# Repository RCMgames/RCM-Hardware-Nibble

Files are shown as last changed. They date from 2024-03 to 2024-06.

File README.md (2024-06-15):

# RCM-Hardware-Nibble
v1.8

Half a [BYTE](https://github.com/RCMgames/RCM-Hardware-BYTE)

* 1.08 by 1.12 inches, 27.432 by 28.448 millimeters
* 4 motors
* 4 servos
* 2 additional GPIO pins
* built-in [IMU](https://github.com/RCMgames/useful-code/blob/main/sensors/IMUs/ICM20948/ICM20948_helper.h)
* battery monitoring
* I2C connector on QT PY
* runs on 3-11 volts

program with [RCMv2](https://github.com/RCMgames/RCMv2)

### Tested with the following types of ESP32 QT Py:
| Type of QT Py | PlatformIO name | link to Adafruit |
| --- | --- | --- |
| S3 with 2MB PSRAM |  adafruit_qtpy_esp32s3_n4r2 |  https://www.adafruit.com/product/5700 |
| S3 with 8Mb Flash |  adafruit_qtpy_esp32s3_nopsram |  https://www.adafruit.com/product/5426 |
| S2 |  adafruit_qtpy_esp32s2 |  https://www.adafruit.com/product/5325  |

Look here for how to program it: https://github.com/RCMgames/RCMv2

Look here for more information and examples of robots: https://github.com/rcmgames

Want slightly larger and 8 motors and 8 servos? Look at the [BYTE](https://github.com/rcmgames/RCM-Hardware-BYTE)

## Options for purchasing

* [PCBWay link](https://www.pcbway.com/project/shareproject/RCMhardwareNibble_v1_8_dbf51cb4.html) (PCBWay will give me a commission without increasing the price for you). (approximately $110 for 2 boards and manufacturing took a month).
* send the gerbers, bill of materials, and ComponentPlacement files (in /PCBproduction-RCM-Nibble) to a PCB manufacturer of your choice (details you may be asked for: min hole 0.25mm, min track/spacing 5/5mil, thickness 1.0mm, 1 oz Cu outer 1.5 oz Cu inner, tell them to not solder the icm20948's exposed pad)

## Components
Solder by hand to complete the assembly of your boards.
| part | links | quantity | notes |
| ----- | ----- | ----- | ----- |
| RCM Nibble circuit board | [options for purchasing](https://github.com/RCMgames/RCM-Hardware-Nibble/tree/main#options-for-purchasing) | 1 | |
| ESP32 QT Py | [compatible QT Py](https://github.com/RCMgames/RCM-Hardware-Nibble/tree/main#tested-with-the-following-types-of-esp32-qt-py) | 1 | |
| 2x4 female header pins | [this](https://www.digikey.com/en/products/detail/sullins-connector-solutions/PPPC042LFBN-RC/810244) or 2 strips of 4 | 1 | for motors |
| 7 female header pins | | 2 | for QT Py |
| 3 male header pins | | 4 | for servos |
| 2 male header pins | | 2 | for extra GPIO pins |
| battery wires | JST RCY OR 9V battery snap | 1 | [Amazon JST RCY](https://www.amazon.com/dp/B00Z04QFN2/) |
| servo buck boost 5v 2A | [Pololu](https://www.pololu.com/product/4085) | 0 or 1 | if you want to supply voltages above or below what servos can accept (supplies other than 5AAs) |

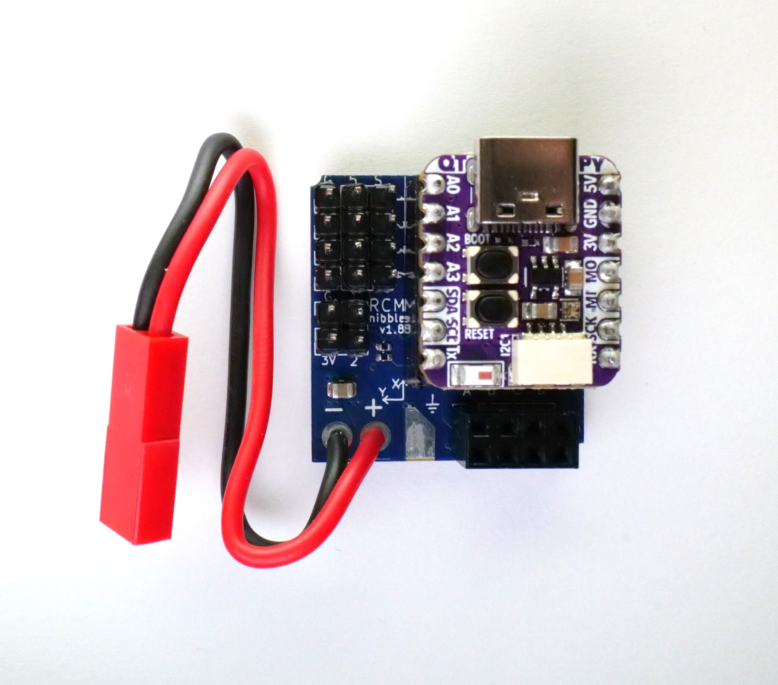
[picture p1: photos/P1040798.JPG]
photos

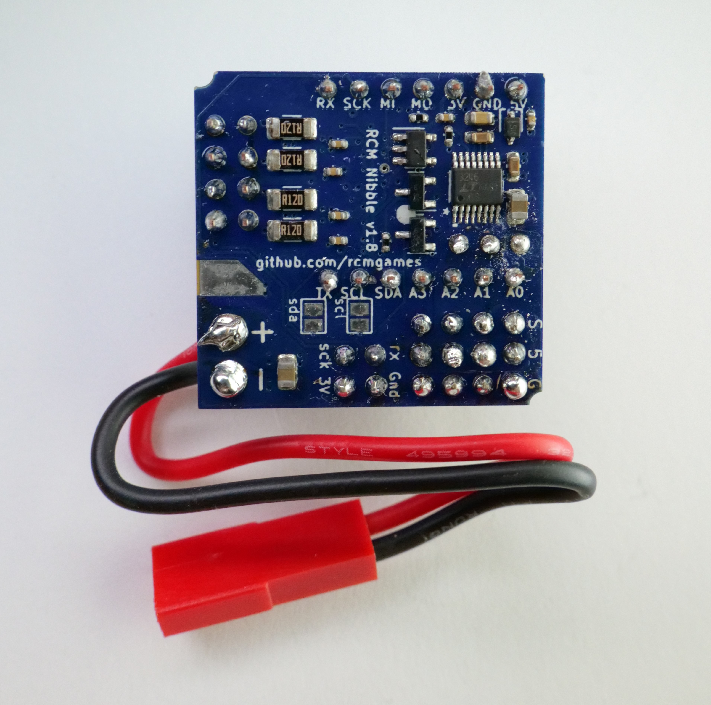
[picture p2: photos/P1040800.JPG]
photos


## Acknowledgements
* I would like to thank [PCBWay](https://www.pcbway.com/) for sponsoring prototyping runs of this project. PCBWay produces very nice boards, supports open source hardware, and gave me great support as I worked on this project. Special thanks to Liam!

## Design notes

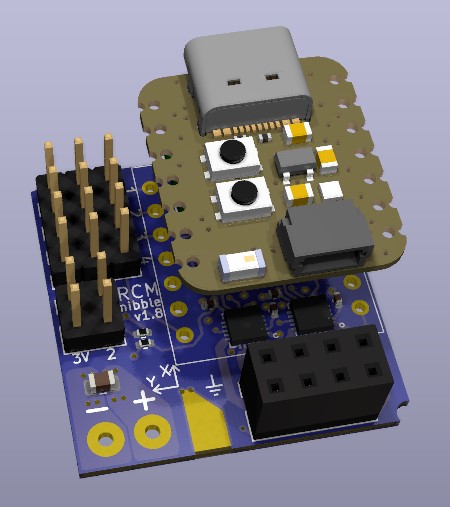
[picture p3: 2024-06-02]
CAD renders/render 1.jpg

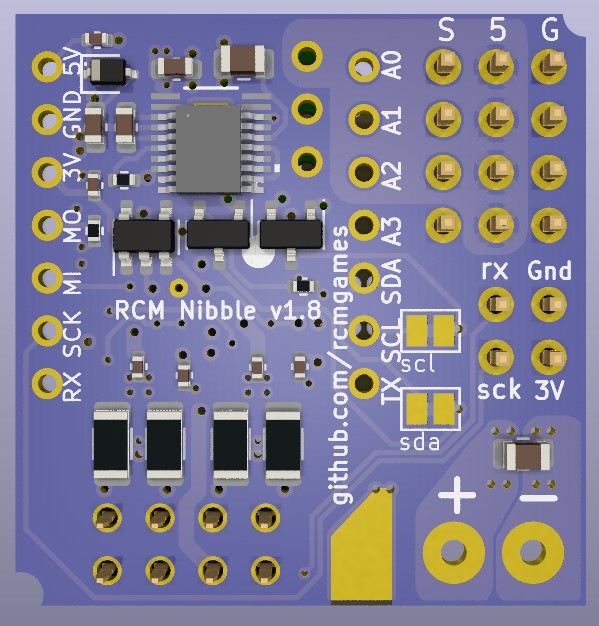
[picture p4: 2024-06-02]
CAD renders/bottom.jpg

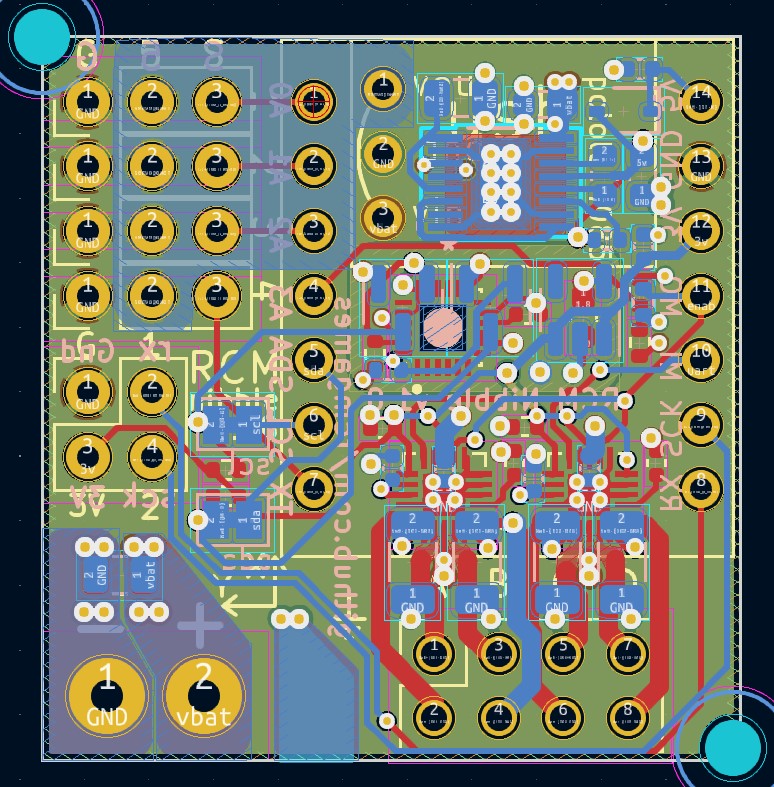
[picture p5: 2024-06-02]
CAD renders/kicad.jpg

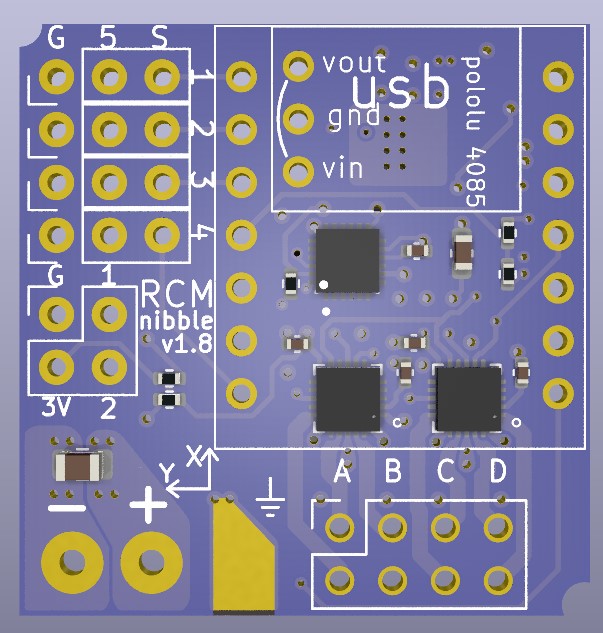
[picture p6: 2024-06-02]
CAD renders/top.jpg

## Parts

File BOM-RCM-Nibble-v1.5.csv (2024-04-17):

Reference | Value | Footprint | Datasheet | Manufacturer | Package | digikey part # | link | mount_type | mpn | Qty
C1, C3-C8, C11, C15, C17, C18 | 100nF/0402/16V/X7R/<=10%/ceramic | Capacitor_SMD:C_0402_1005Metric | ~ | any | 0402 | 4713-GMC04X7R104K50NTCT-ND | https://www.digikey.cn/en/products/detail/cal-chip-electronics-inc/GMC04X7R104K50NT/18151122 | smt | GMC04X7R104K50NT | 11
C2, C9, C16 | 22uF/0805/>=16V | Capacitor_SMD:C_0805_2012Metric | ~ | any | 0805 | 4713-GMC21X5R226M25NTCT-ND | https://www.digikey.cn/en/products/detail/cal-chip-electronics-inc/GMC21X5R226M25NT/18151071 | smt | GMC21X5R226M25NT | 3
C10, C13, C14 | 2.2uF/0603/>=16V | Capacitor_SMD:C_0603_1608Metric | ~ | any | 0603 | 4713-GMC10X7R225K16NTCT-ND | https://www.digikey.cn/en/products/detail/cal-chip-electronics-inc/GMC10X7R225K16NT/22461333 | smt | GMC10X7R225K16NT | 3
C12 | 22uF/0603/>=10V | Capacitor_SMD:C_0603_1608Metric | ~ | any | 0603 | 4713-GMC10X5R226M10NTCT-ND | https://www.digikey.cn/en/products/detail/cal-chip-electronics-inc/GMC10X5R226M10NT/22461275 | smt | GMC10X5R226M10NT | 1
D1 | 1A Zener Diode / >=1A / 600 mV Vf @ 1 A | Diode_SMD:D_SOD-323 | ~ | Good-Ark Semiconductor | D_SOD-323 | 4786-GDB5818WSCT-ND | https://www.digikey.com/en/products/detail/good-ark-semiconductor/GDB5818WS/18648294 | smt | GDB5818WS | 1
ESP32_QT_PY1 | microcontroller | !RCMhardware footprints:ESP32 QT PY | ~ | do not place or purchase for PCB assembly | tht | 1528-5426-ND or 1528-5700-ND |  | tht | do not place or purchase for PCB assembly | 1
H1, H2 | MountingHole | MountingHole:MountingHole_2.2mm_M2 | ~ | n/a | n/a | n/a | n/a | n/a | n/a | 2
IC1, IC2 | TMC7300 | !RCMhardware footprints:QFN-20-1EP_3x3mm_P0.4mm_EP1.65x1.65mm | https://www.analog.com/media/en/technical-documentation/data-sheets/TMC7300_datasheet_rev1.08.pdf | Analog Devices | QFN-20-1EP_3x3mm_P0.4mm_EP1.65x1.65mm | 175-TMC7300-LA-TCT-ND | https://www.digikey.com/en/products/detail/analog-devices-inc-maxim-integrated/TMC7300-LA-T/11483537 | smt | TMC7300-LA-T | 2
J1 | pads to solder wires to | !RCMhardware footprints:battery wires | JST RCY suggested | ~ | tht | ~ | https://www.amazon.com/dp/B00Z04QFN2/ | tht | do not place or purchase for PCB assembly | 1
J2-J5 | Conn_01x03 | Connector_PinHeader_2.54mm:PinHeader_1x03_P2.54mm_Vertical | ~ | ~ | tht | ~ | ~ | tht | do not place or purchase for PCB assembly | 4
J6 | 2x04 female header pins | !RCMhardware footprints:PinSocket_2x04_P2.54mm_Vertical | ~ | do not place or purchase for PCB assembly | tht | S7107-ND | https://www.digikey.com/en/products/detail/sullins-connector-solutions/PPTC082LFBN-RC/810214 | tht | do not place or purchase for PCB assembly | 1
J9 | Conn_02x02_Top_Bottom | Connector_PinHeader_2.54mm:PinHeader_2x02_P2.54mm_Vertical | ~ | do not place or purchase for PCB assembly | tht | ~ | ~ | tht | do not place or purchase for PCB assembly | 1
NT1, NT2 | NetTie_2 | Jumper:SolderJumper-2_P1.3mm_Bridged_Pad1.0x1.5mm | ~ | n/a | n/a | n/a | n/a | tht | do not place or purchase for PCB assembly | 2
Q3, Q4 | BSS138, N channel mosfet >=0.22A | Package_TO_SOT_SMD:SOT-23 | https://www.onsemi.com/pub/Collateral/BSS138-D.PDF | onsemi | SOT-23 | BSS138CT-ND | https://www.digikey.com/en/products/detail/onsemi/BSS138/244210 | smt | BSS138 | 2
R1 | 30k / <=1% | Resistor_SMD:R_0402_1005Metric | ~ | any | 0402 | CR0402-FX-3002GLFCT-ND | https://www.digikey.com/en/products/detail/bourns-inc/CR0402-FX-3002GLF/3783296 | smt | CR0402-FX-3002GLF | 1
R2, R7, R9-R13 | 10k / <=1% | Resistor_SMD:R_0402_1005Metric | ~ | any | 0402 | CR0402-FX-1002GLFCT-ND | https://www.digikey.com/en/products/detail/bourns-inc/CR0402-FX-1002GLF/3593192 | smt | CR0402-FX-1002GLF | 7
R3-R6 | 120mΩ / 0.5W / 1206 / <=1% | Resistor_SMD:R_1206_3216Metric | ~ | any | 1206 | CRL1206-FW-R120ELFCT-ND | https://www.digikey.com/en/products/detail/bourns-inc/CRL1206-FW-R120ELF/3785719 | smt | CRL1206-FW-R120ELF | 4
U1 | pololu 4085 | !RCMhardware footprints:pololu 4085 | ~ | Pololu | tht | 2183-4085-ND | https://www.digikey.com/en/products/detail/pololu-corporation/4085/16164508 | tht | do not place or purchase for PCB assembly | 1
U2 | LTC3246EMSE-PBF / 500mA charge pump | !RCMhardware footprints:MSE_16_ADI | LTC3246EMSE-PBF | Analog Devices | 16-TFSOP (0.118", 3.00mm Width) Exposed Pad | LTC3246EMSE#PBF-ND | https://www.digikey.com/en/products/detail/analog-devices-inc/LTC3246EMSE-PBF/7363792 | smt | LTC3246EMSE#PBF | 1
U3 | ICM-20948 | !RCMhardware footprints:QFN40P300X300X105-24N | https://invensense.tdk.com/wp-content/uploads/2016/06/DS-000189-ICM-20948-v1.3.pdf | TDK InvenSense | 24-QFN (3x3) | 1428-1123-1-ND | https://www.digikey.com/en/products/detail/tdk-invensense/ICM-20948/6623535 | smt | ICM-20948 | 1
U4 | MIC5225-1.8V | Package_TO_SOT_SMD:SOT-23-5 | https://ww1.microchip.com/downloads/en/DeviceDoc/mic5225.pdf | Microchip | SC-74A, SOT-753 | 576-3017-1-ND | https://www.digikey.com/en/products/detail/microchip-technology/MIC5225-1-8YM5-TR/1834695 | smt | MIC5225-1.8YM5-TR | 1

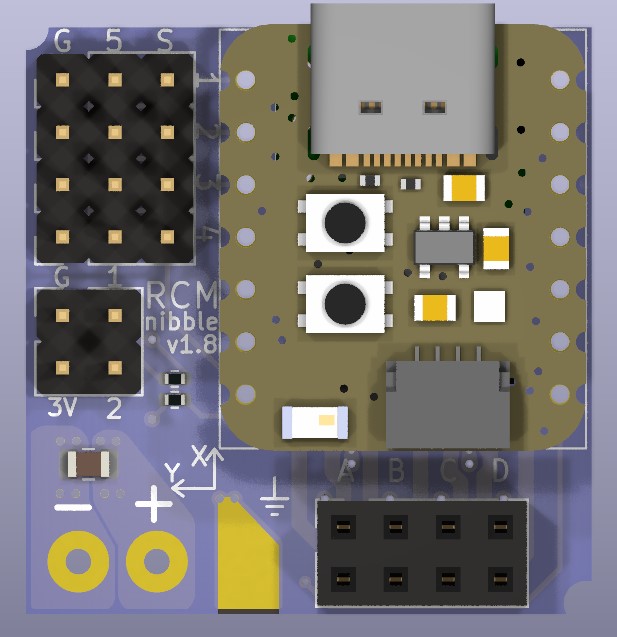
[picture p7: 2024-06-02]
CAD renders/top with components.jpg

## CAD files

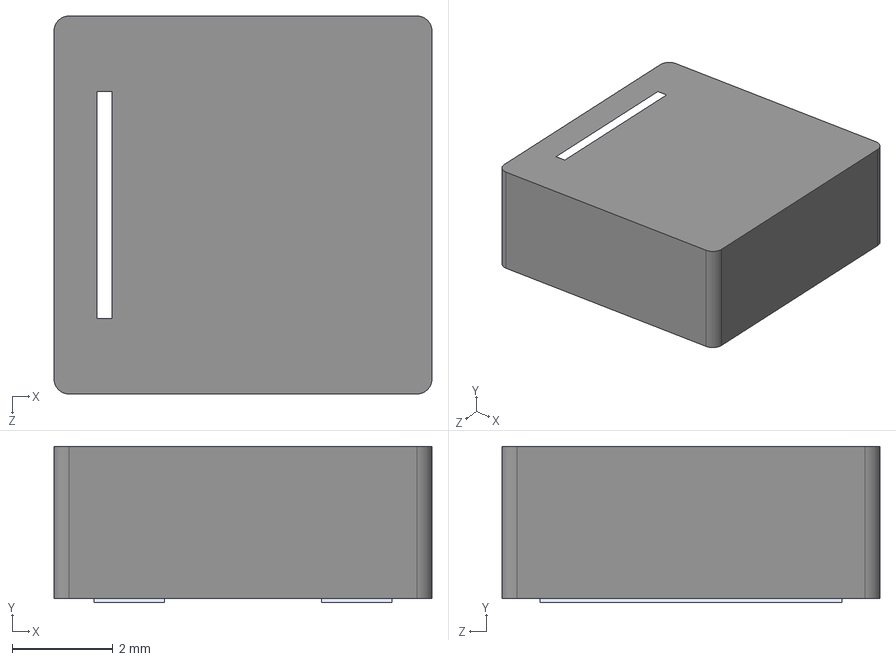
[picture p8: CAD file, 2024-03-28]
KICAD-RCM-Nibble/!RCMhardware footprints/XAL7030-472MEC.step
7.50 x 3.10 x 7.50 mm

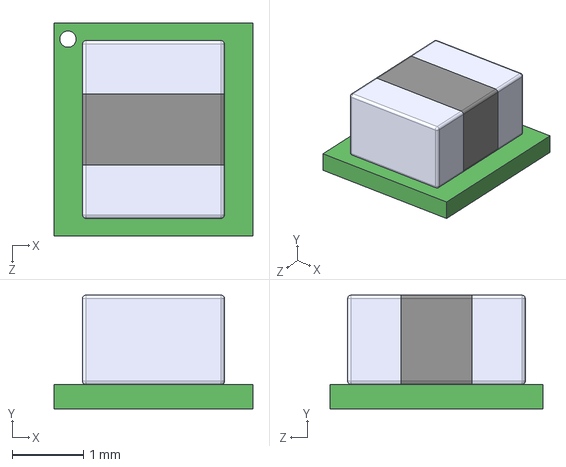
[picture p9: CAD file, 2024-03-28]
KICAD-RCM-Nibble/!RCMhardware footprints/TPSM82903SISR--3DModel-STEP-56544.STEP
2.80 x 1.60 x 3.00 mm

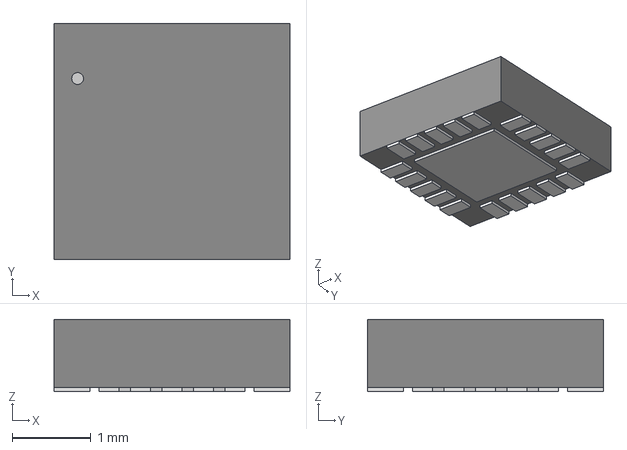
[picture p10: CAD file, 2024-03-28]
KICAD-RCM-Nibble/!RCMhardware footprints/QFN20_3x3_TRI.step
3.00 x 3.00 x 0.917 mm

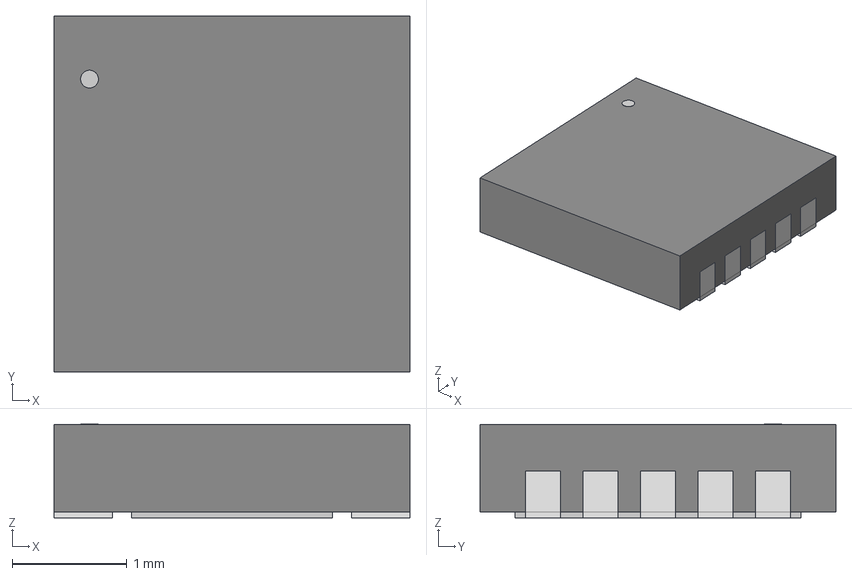
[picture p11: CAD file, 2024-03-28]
KICAD-RCM-Nibble/!RCMhardware footprints/DFN-10_DD_LIT.step
3.10 x 3.10 x 0.815 mm

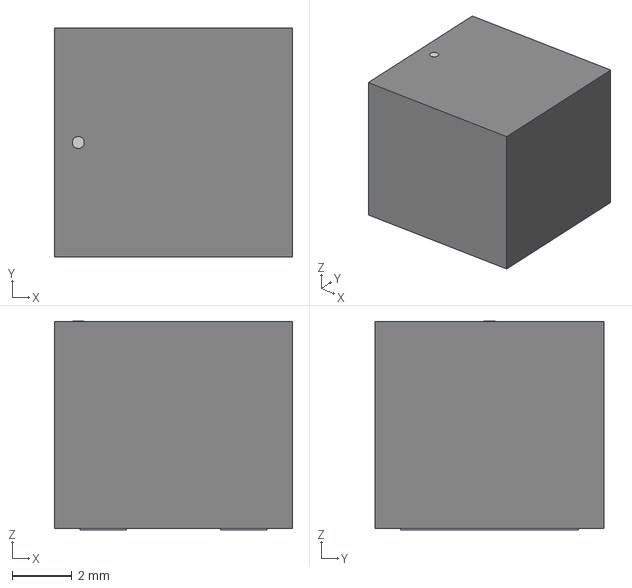
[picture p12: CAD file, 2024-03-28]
KICAD-RCM-Nibble/!RCMhardware footprints/IND_XAL7070_COC.step
8.00 x 7.70 x 7.01 mm

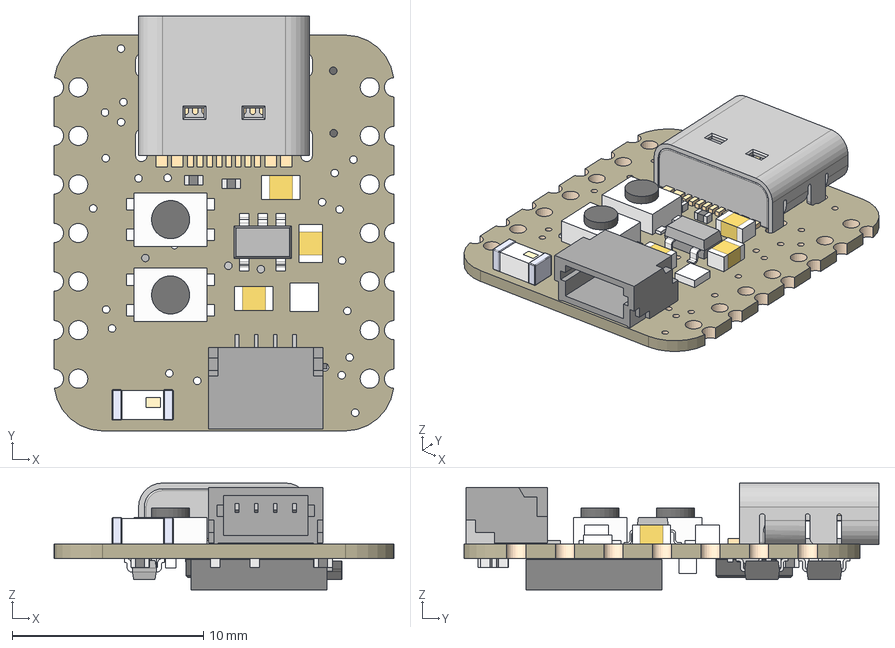
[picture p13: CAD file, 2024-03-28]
KICAD-RCM-Nibble/!RCMhardware footprints/5395 QT Py ESP32 PICO.step
17.8 x 21.7 x 5.59 mm
Board
22uF x 3
BOOT0 x 2
10K x 14
USB TYPE C
STEMMA_I2C_QTSKINNY
AP2112K-3.3
WS2812B_SK6805_1515
NSR0320 x 2
2.2nH
2.4GHz
1uF
ESP-32-PICO-V3-02
CP2102N-24
DUAL NPN

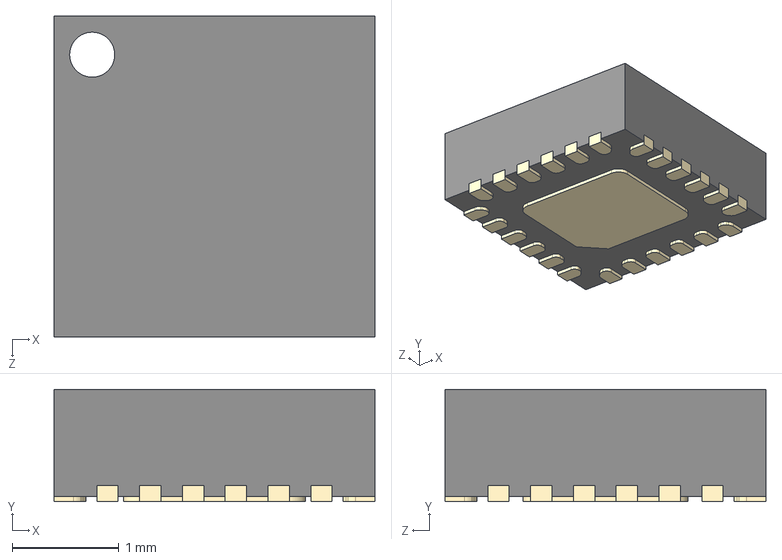
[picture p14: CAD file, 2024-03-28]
KICAD-RCM-Nibble/!RCMhardware footprints/ICM-20948.step
3.00 x 1.05 x 3.00 mm

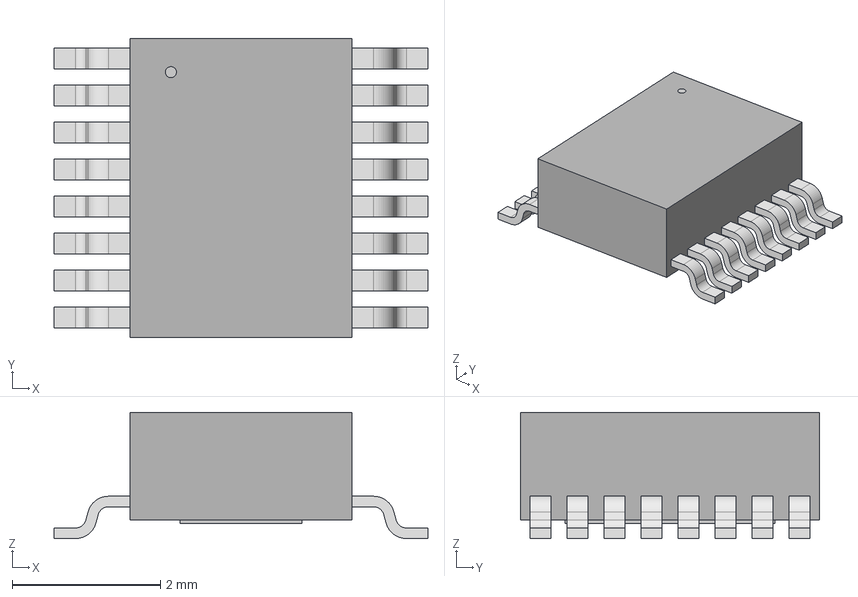
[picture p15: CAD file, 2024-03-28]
KICAD-RCM-Nibble/!RCMhardware footprints/MSE_16_ADI.step
5.05 x 4.04 x 1.70 mm

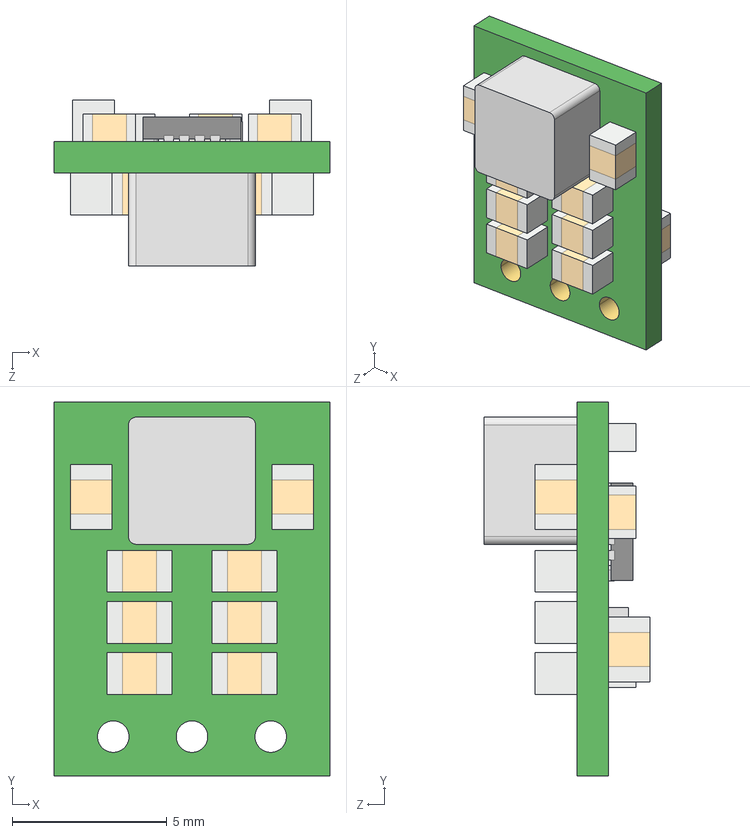
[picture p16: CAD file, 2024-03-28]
KICAD-RCM-Nibble/!RCMhardware footprints/pololu 4085 5v-2a-step-up-step-down-voltage-regulator-s13v20f5.step
8.89 x 12.1 x 5.37 mm

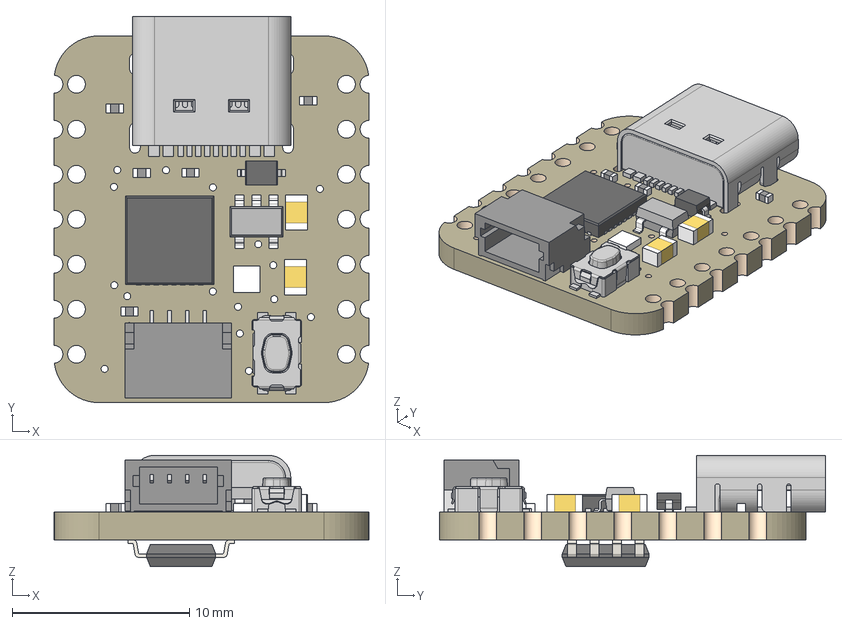
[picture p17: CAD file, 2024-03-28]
KICAD-RCM-Nibble/!RCMhardware footprints/4600 QTPy.step
17.8 x 21.8 x 6.28 mm
Board
10uF x 2
reset
ATSAMD21E
TPB1,27
5.1K x 5
USB TYPE C
STEMMA_I2C_QTSKINNY
AP2112K-3.3
WS2812B_SK6805_1515
NSR0320
SOIC8_150MIL

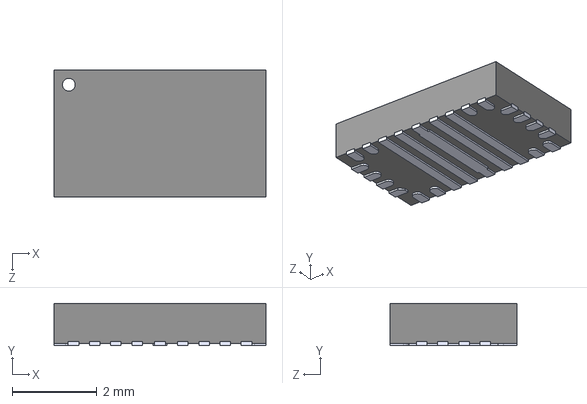
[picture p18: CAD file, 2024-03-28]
KICAD-RCM-Nibble/!RCMhardware footprints/TPS552892RYQR.step
5.00 x 1.00 x 3.00 mm

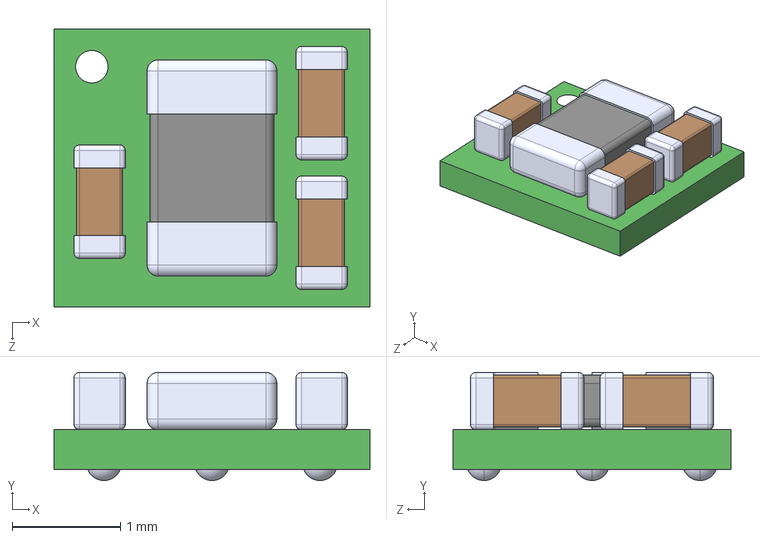
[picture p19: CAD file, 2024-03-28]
KICAD-RCM-Nibble/!RCMhardware footprints/TPS81256SIPT--3DModel-STEP-56544.STEP
2.92 x 1.00 x 2.58 mm

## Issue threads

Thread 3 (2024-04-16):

[not a problemC12 part number doesn't meet specifications in description

joshua-8, 2024-04-16:
schematic specifies >=16 Volts for C12, but specifies a part number that is only rated for 10 Volts. Only 5 volts is required so it’s not a problem.

Closed 2024-04-16.

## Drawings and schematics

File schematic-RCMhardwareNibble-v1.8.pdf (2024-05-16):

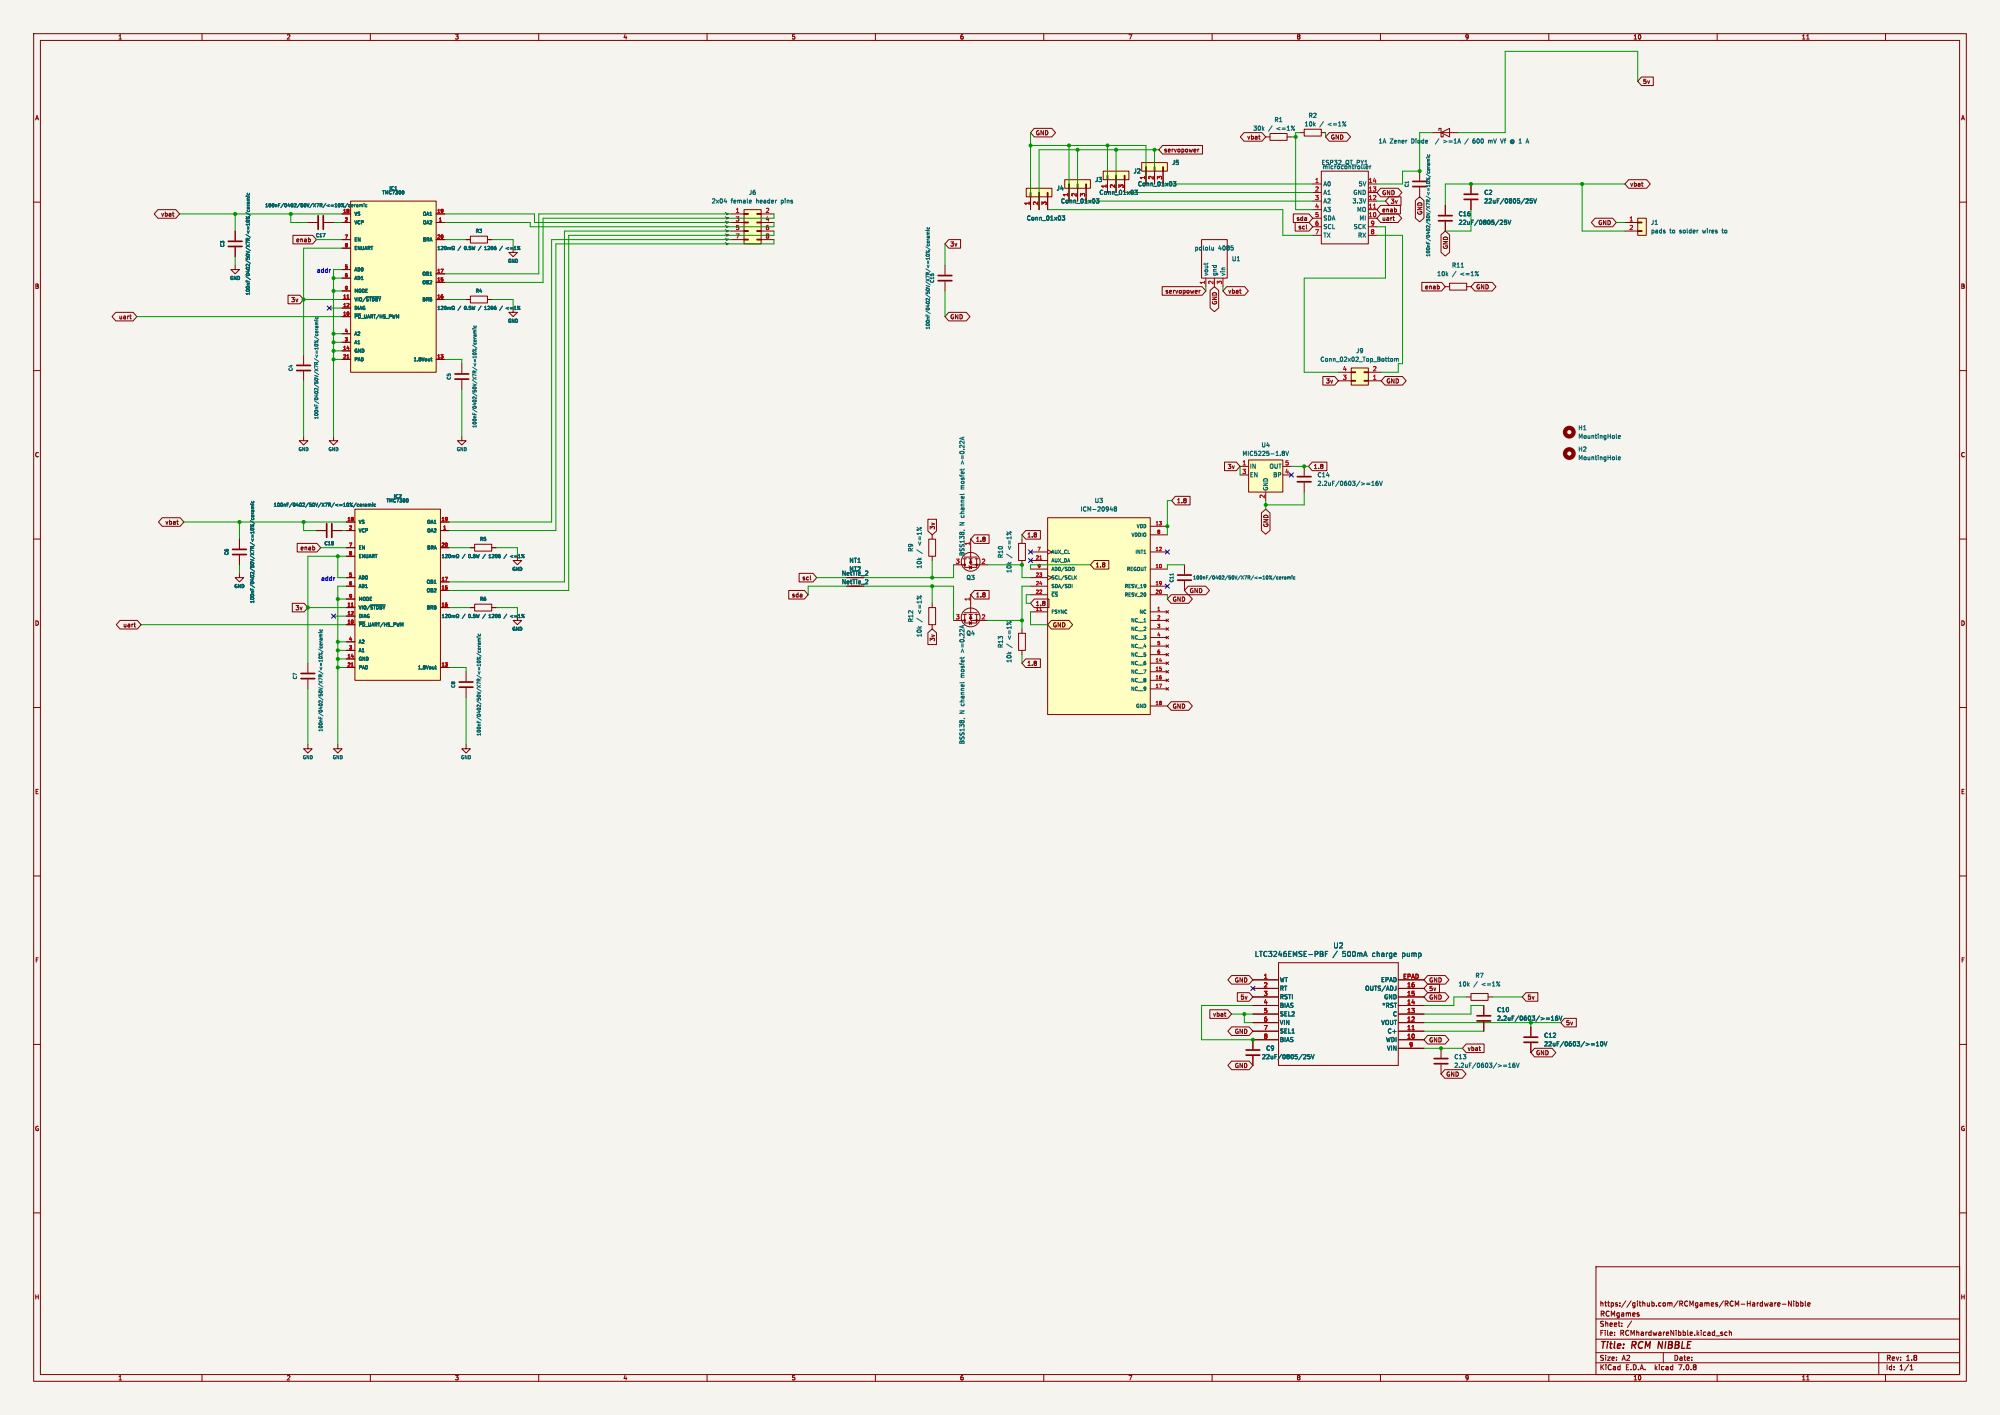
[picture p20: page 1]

pads to solder wires to R1

File: RCMhardwareNibble.kicad_sch Sheet: / RCMgames

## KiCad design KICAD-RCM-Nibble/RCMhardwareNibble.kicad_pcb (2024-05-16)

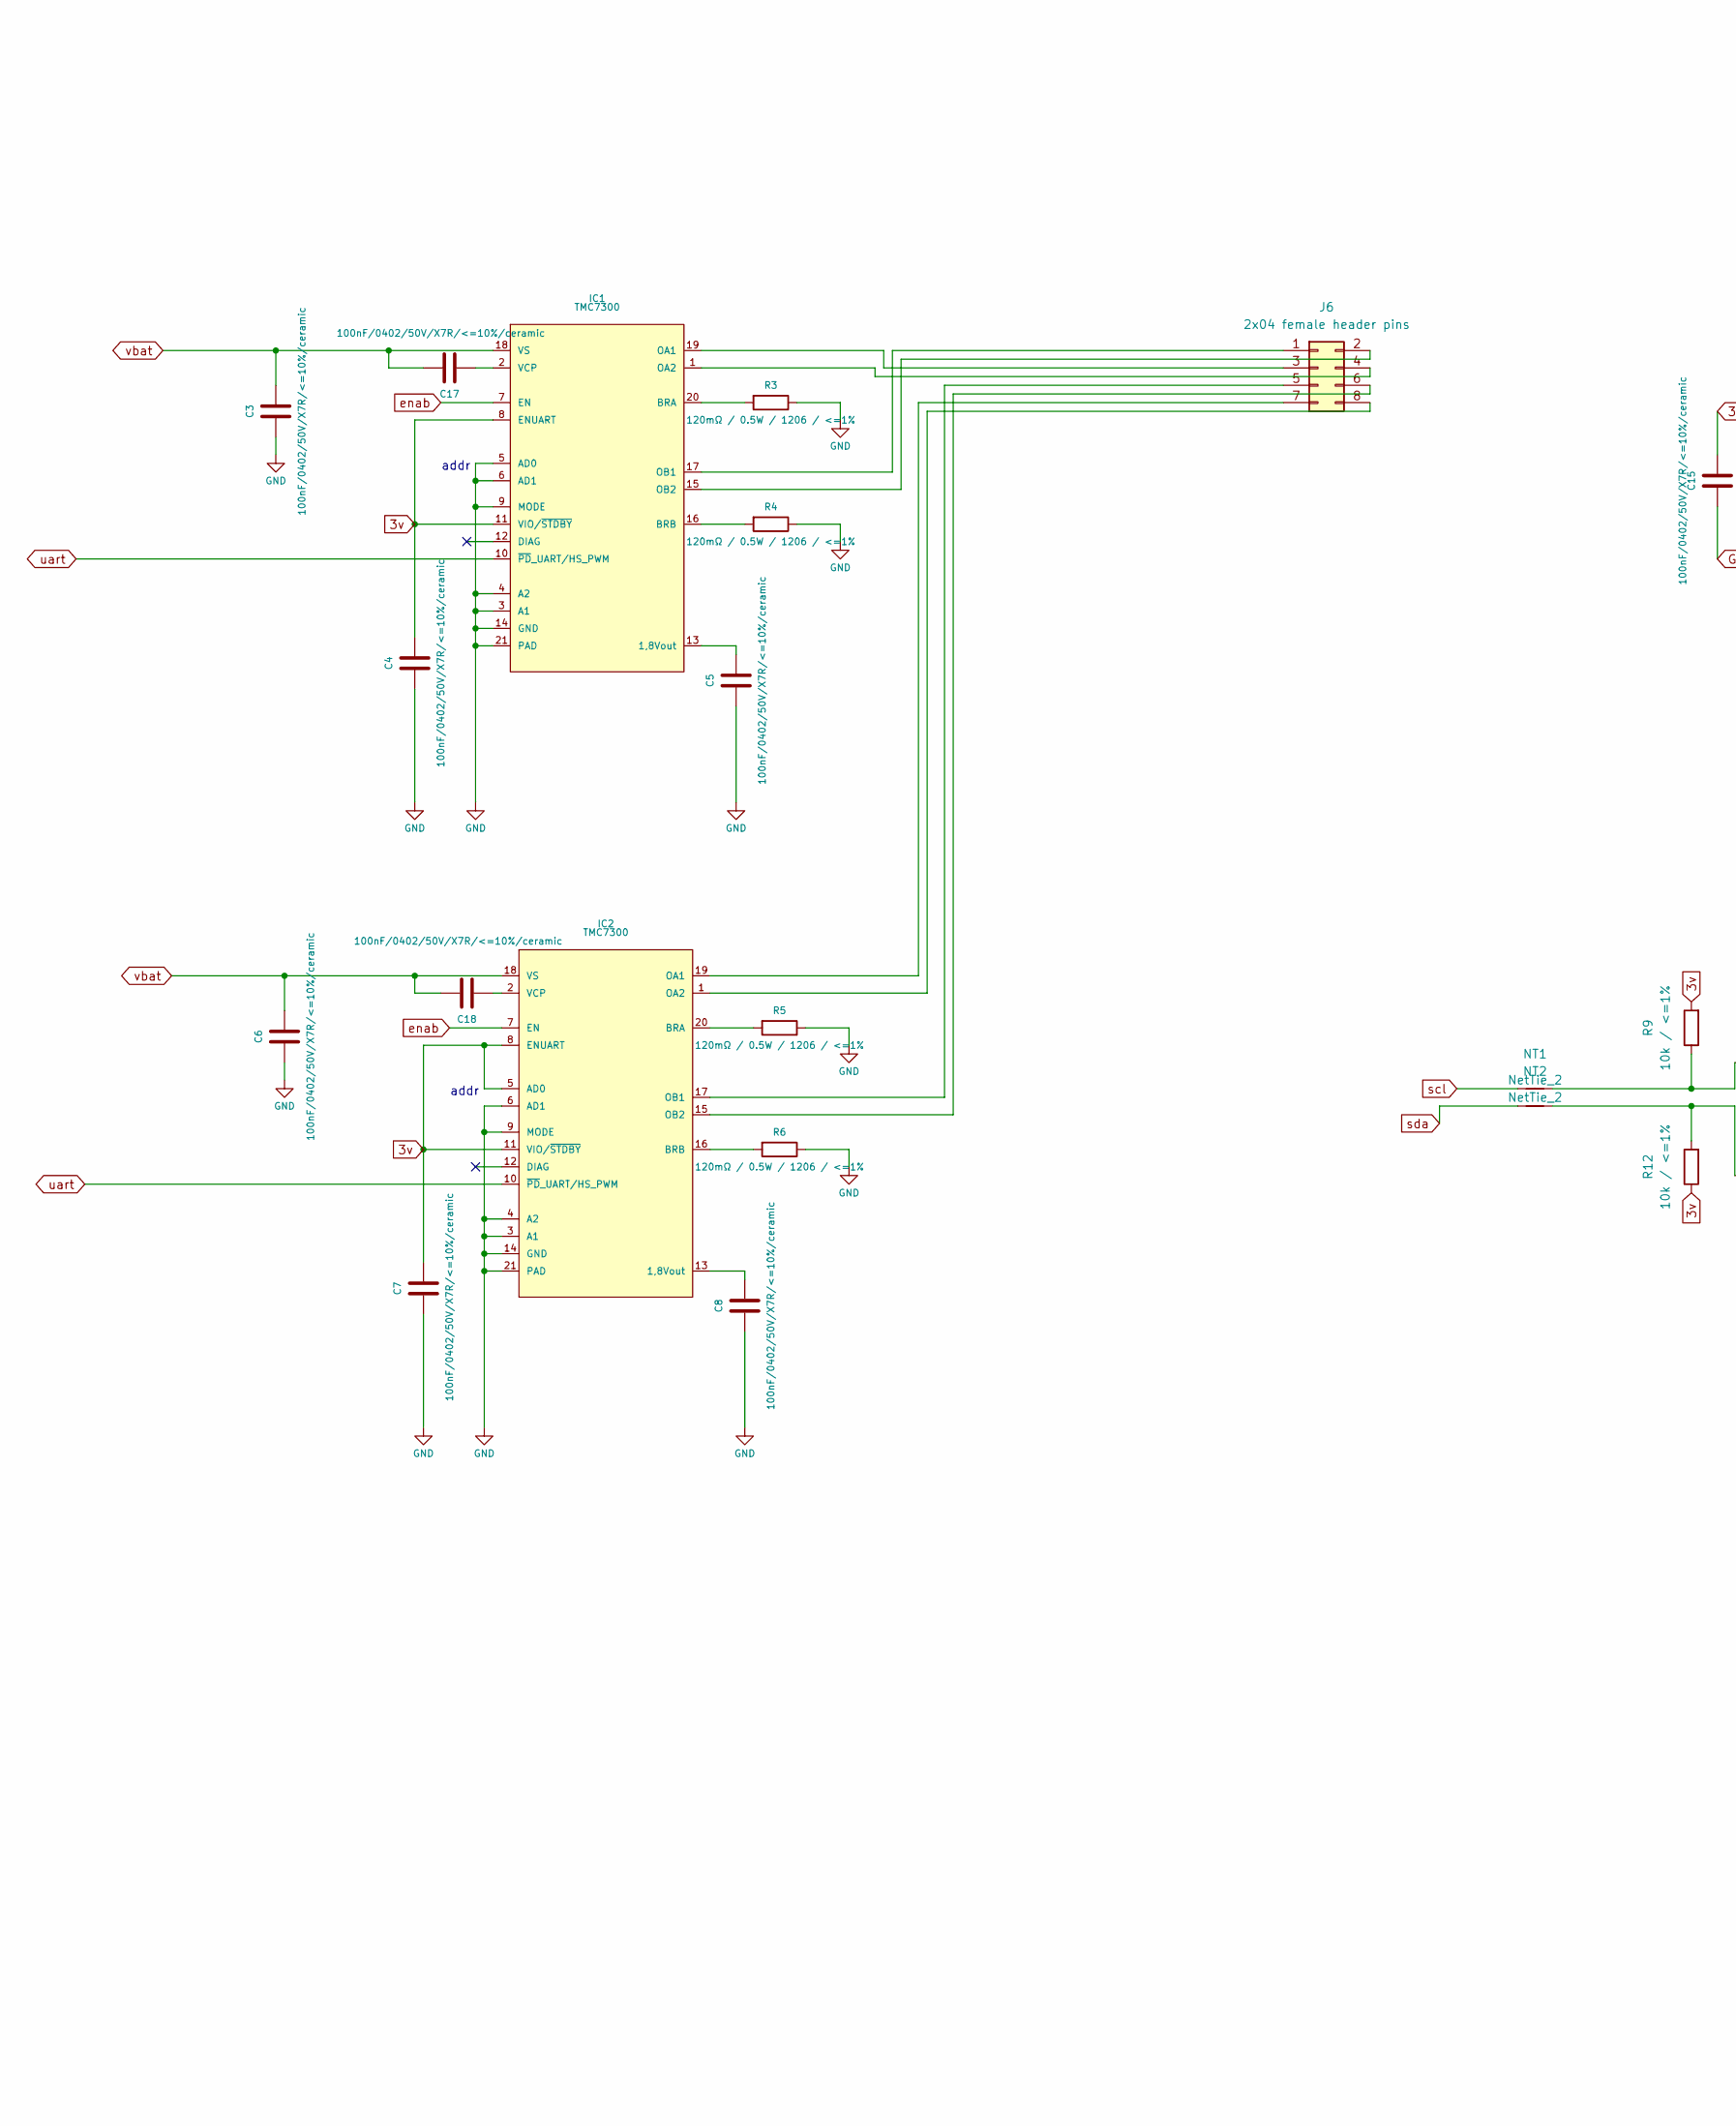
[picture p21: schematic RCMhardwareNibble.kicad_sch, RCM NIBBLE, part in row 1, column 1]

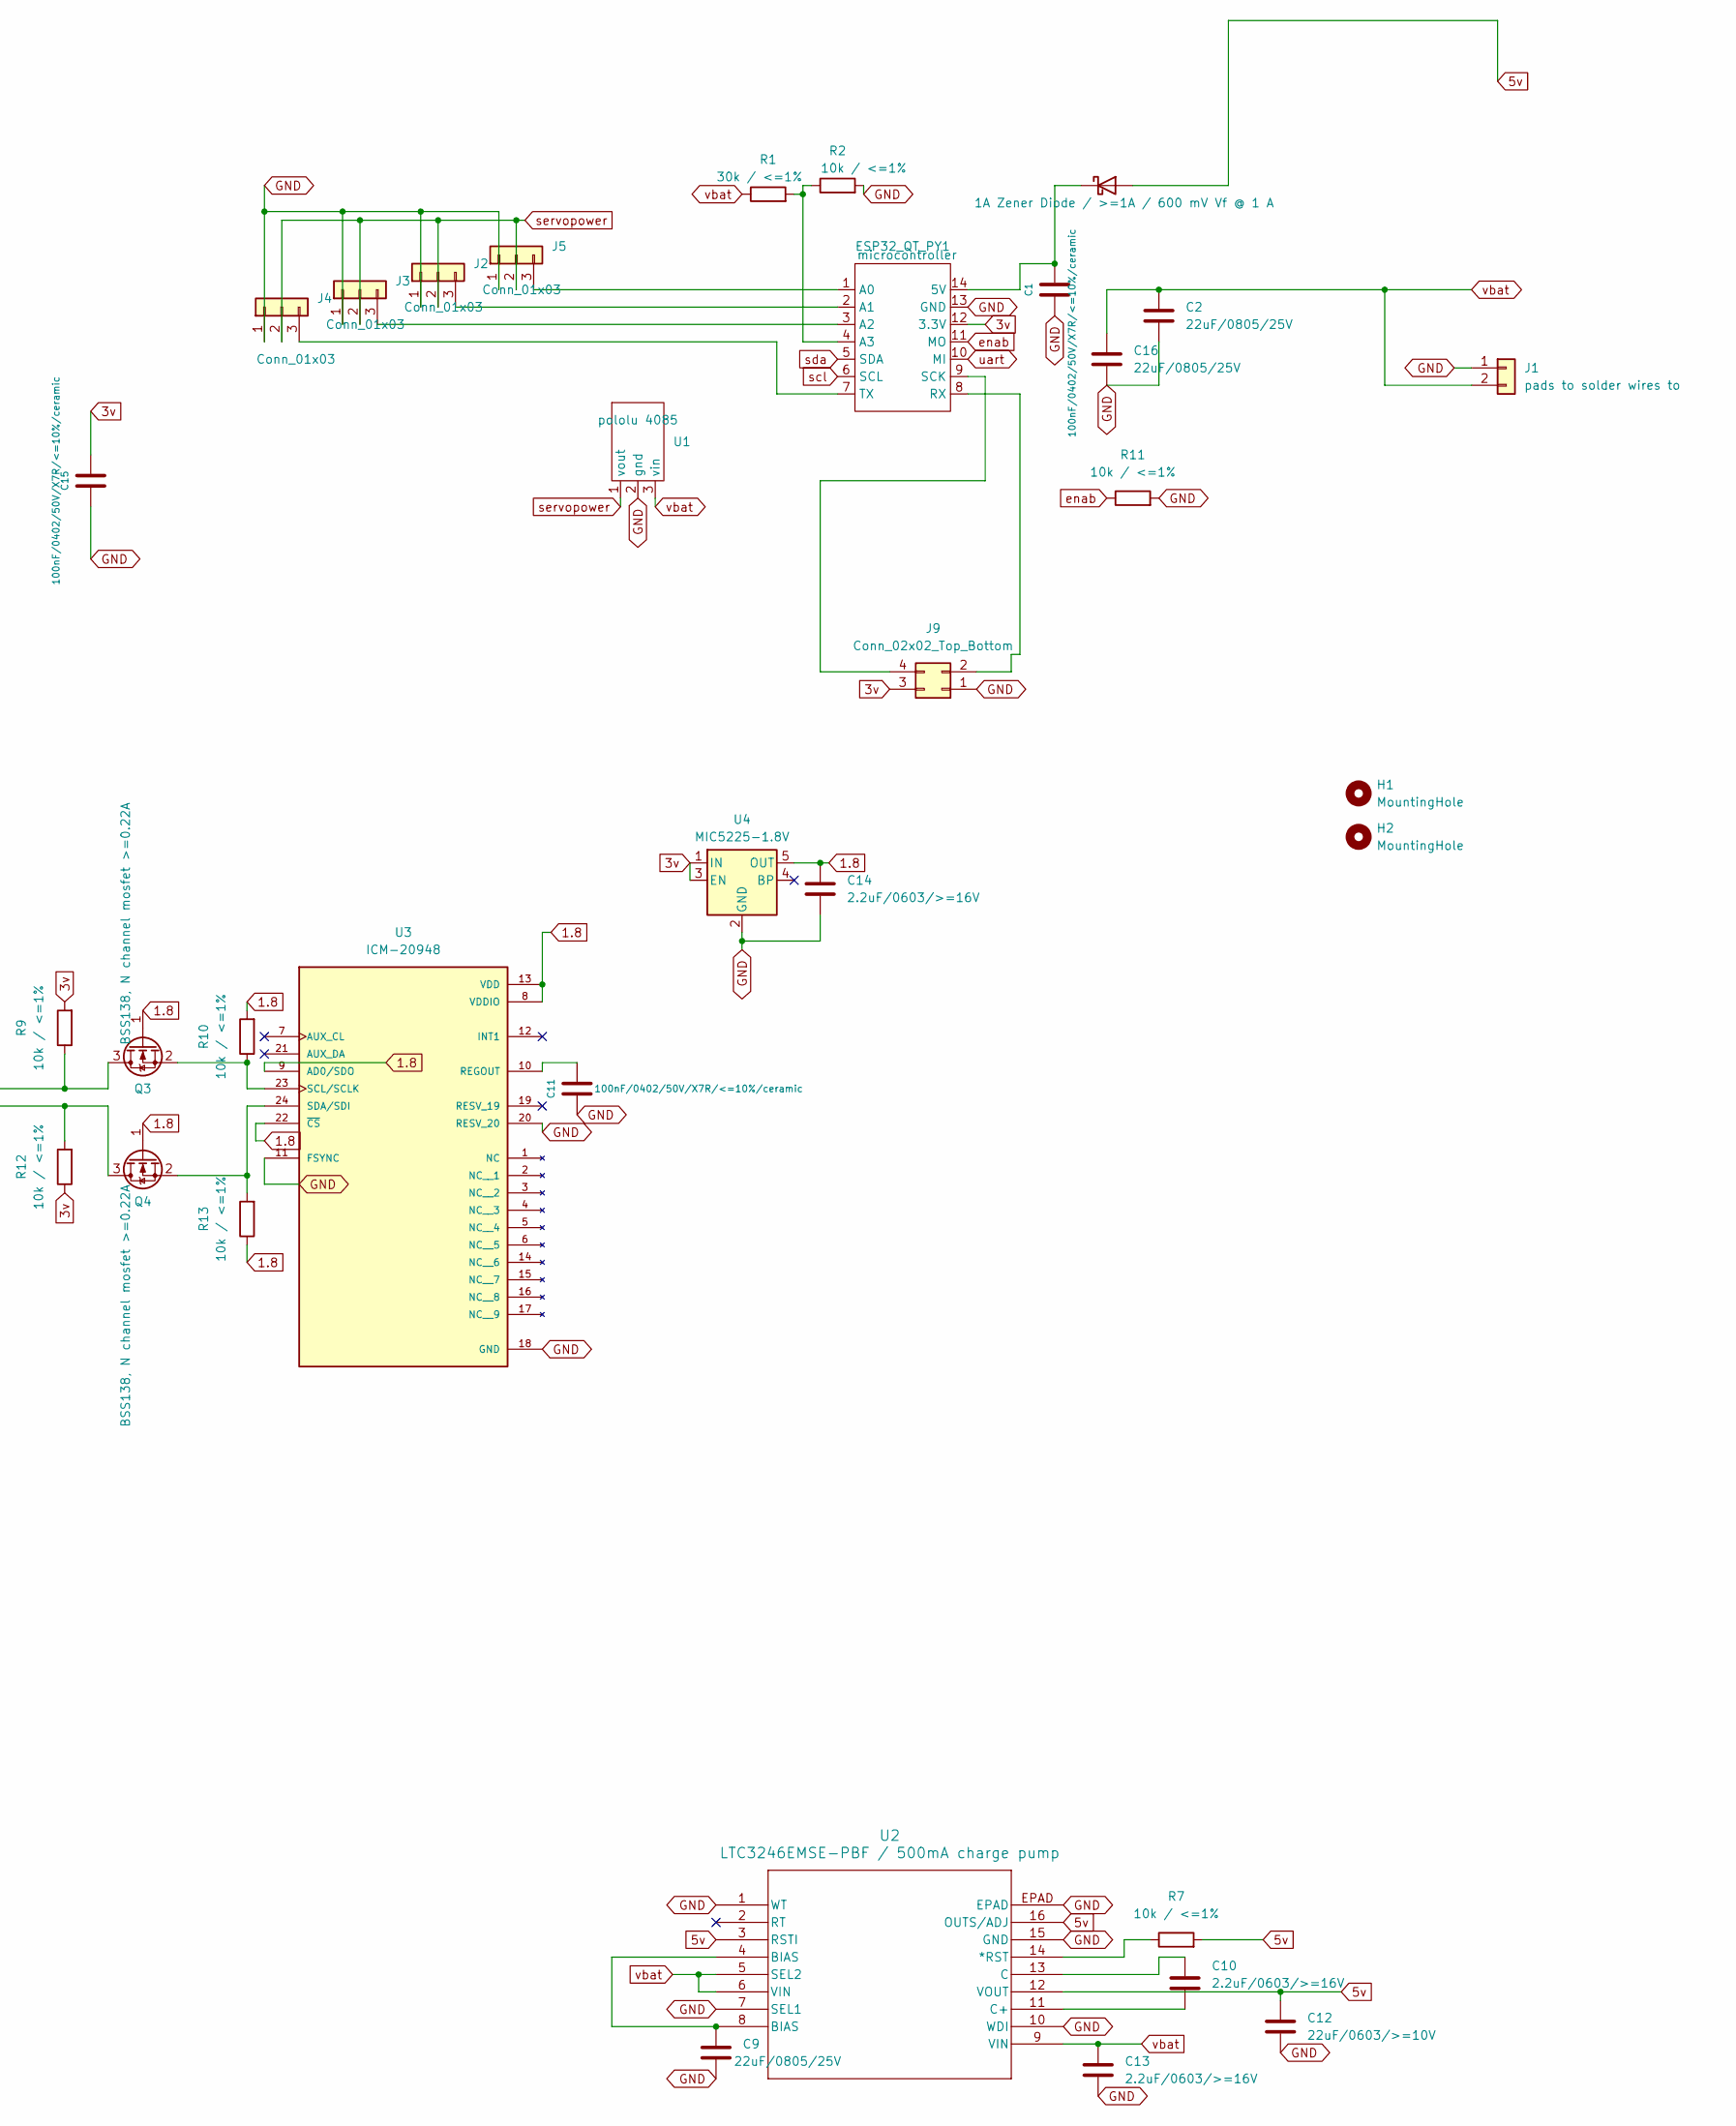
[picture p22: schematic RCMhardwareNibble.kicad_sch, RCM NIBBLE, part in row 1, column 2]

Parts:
C1, C3, C4, C5, C6, C7, C8, C11, C15, C17, C18: 100nF/0402/50V/X7R/<=10%/ceramic; C_0402_1005Metric; mpn GMC04X7R104K50NT; digikey part # 4713-GMC04X7R104K50NTCT-ND
C2, C9, C16: 22uF/0805/25V; C_0805_2012Metric; mpn GMC21X5R226M25NT; digikey part # 4713-GMC21X5R226M25NTCT-ND
C10, C13, C14: 2.2uF/0603/>=16V; C_0603_1608Metric; mpn GMC10X7R225K16NT; digikey part # 4713-GMC10X7R225K16NTCT-ND
C12: 22uF/0603/>=10V; C_0603_1608Metric; mpn GMC10X5R226M10NT; digikey part # 4713-GMC10X5R226M10NTCT-ND
D1: 1A Zener Diode / >=1A / 600 mV Vf @ 1 A; D_SOD-323; mpn GDB5818WS; digikey part # 4786-GDB5818WSCT-ND
ESP32_QT_PY1: microcontroller; ESP32 QT PY; mpn do not place or purchase for PCB assemb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; digikey part # 1528-5426-ND or 1528-5700-ND
H1, H2: MountingHole; MountingHole_2.2mm_M2; mpn DNP; digikey part # n/a
IC1, IC2: TMC7300; QFN-20-1EP_3x3mm_P0.4mm_EP1.65x1.65mm; mpn TMC7300-LA-T; digikey part # 175-TMC7300-LA-TCT-ND
J1: pads to solder wires to; battery wires; mpn do not place or purchase for PCB assemb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
J2, J3, J4, J5: Conn_01x03; PinHeader_1x03_P2.54mm_Vertical; mpn do not place or purchase for PCB assemb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
J6: 2x04 female header pins; PinSocket_2x04_P2.54mm_Vertical; mpn do not place or purchase for PCB assemb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; digikey part # S7107-ND
J9: Conn_02x02_Top_Bottom; PinHeader_2x02_P2.54mm_Vertical; mpn do not place or purchase for PCB assemb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
NT1, NT2: NetTie_2; SolderJumper-2_P1.3mm_Bridged_Pad1.0x1.5mm; mpn do not place or purchase for PCB assemb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; digikey part # n/a
Q3, Q4: BSS138, N channel mosfet >=0.22A; SOT-23; mpn BSS138; digikey part # BSS138CT-ND
R1: 30k / <=1%; R_0402_1005Metric; mpn CR0402-FX-3002GLF; digikey part # CR0402-FX-3002GLFCT-ND
R2, R7, R9, R10, R11, R12, R13: 10k / <=1%; R_0402_1005Metric; mpn CR0402-FX-1002GLF; digikey part # CR0402-FX-1002GLFCT-ND
R3, R4, R5, R6: 120mΩ / 0.5W / 1206 / <=1%; R_1206_3216Metric; mpn CRL1206-FW-R120ELF; digikey part # CRL1206-FW-R120ELFCT-ND
U1: pololu 4085; mpn do not place or purchase for PCB assemb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; digikey part # 2183-4085-ND
U2: LTC3246EMSE-PBF / 500mA charge pump; MSE_16_ADI; mpn LTC3246EMSE#PBF; digikey part # LTC3246EMSE#PBF-ND
U3: ICM-20948; QFN40P300X300X105-24N; mpn ICM-20948; digikey part # 1428-1123-1-ND
U4: MIC5225-1.8V; SOT-23-5; mpn MIC5225-1.8YM5-TR; digikey part # 576-3017-1-ND

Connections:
1.8: C14.1, Q3.1 (G), Q4.1 (G), R10.2, R13.1, U3.8 (VDDIO), U3.9 (AD0/SDO), U3.13 (VDD), U3.22 (~CS), U4.5 (OUT)
3v: C4.1, C7.1, C15.1, ESP32_QT_PY1.12 (3.3V), IC1.8 (ENUART), IC1.11 (VIO/~STDBY), IC2.5 (AD0), IC2.8 (ENUART), IC2.11 (VIO/~STDBY), J9.3, R9.2, R12.1, U4.1 (IN), U4.3 (EN)
5v: C12.2, D1.2 (A), R7.2, U2.3 (RSTI), U2.12 (VOUT), U2.16 (OUTS/ADJ)
GND: C1.2, C2.2, C3.2, C4.2, C5.2, C6.2, C7.2, C8.2, C9.1, C11.2, C12.1, C13.2, C14.2, C15.2, C16.2, ESP32_QT_PY1.13 (GND), IC1.3 (A1), IC1.4 (A2), IC1.5 (AD0), IC1.6 (AD1), IC1.9 (MODE), IC1.14 (GND), IC1.21 (PAD), IC2.3 (A1), IC2.4 (A2), IC2.6 (AD1), IC2.9 (MODE), IC2.14 (GND), IC2.21 (PAD), J1.1, J2.1, J3.1, J4.1, J5.1, J9.1, R2.2, R3.1, R4.1, R5.1, R6.1, R11.2, U1.2 (gnd), U2.1 (WT), U2.7 (SEL1), U2.10 (WDI), U2.15 (GND), U2.EPAD, U3.11 (FSYNC), U3.18 (GND), U3.20 (RESV_20), U4.2 (GND)
unnamed: C9.2, U2.4 (BIAS), U2.8 (BIAS)
unnamed: C1.1, D1.1 (K), ESP32_QT_PY1.14 (5V)
unnamed: ESP32_QT_PY1.1 (A0), J5.3
unnamed: ESP32_QT_PY1.2 (A1), J2.3
unnamed: ESP32_QT_PY1.3 (A2), J3.3
unnamed: ESP32_QT_PY1.4 (A3), R1.2, R2.1
unnamed: ESP32_QT_PY1.8 (RX), J9.2
unnamed: ESP32_QT_PY1.9 (SCK), J9.4
unnamed: ESP32_QT_PY1.7 (TX), J4.3
unnamed: C5.1, IC1.13 (1,8Vout)
unnamed: IC1.20 (BRA), R3.2
unnamed: IC1.16 (BRB), R4.2
unnamed: IC1.19 (OA1), J6.3
unnamed: IC1.1 (OA2), J6.4
unnamed: IC1.17 (OB1), J6.1
unnamed: IC1.15 (OB2), J6.2
unnamed: C17.2, IC1.2 (VCP)
unnamed: C8.1, IC2.13 (1,8Vout)
unnamed: IC2.20 (BRA), R5.2
unnamed: IC2.16 (BRB), R6.2
unnamed: IC2.19 (OA1), J6.7
unnamed: IC2.1 (OA2), J6.8
unnamed: IC2.17 (OB1), J6.5
unnamed: IC2.15 (OB2), J6.6
unnamed: C18.2, IC2.2 (VCP)
unnamed: NT1.2, Q3.3 (D), R9.1
unnamed: Q3.2 (S), R10.1, U3.23 (SCL/SCLK)
unnamed: NT2.2, Q4.3 (D), R12.2
unnamed: Q4.2 (S), R13.2, U3.24 (SDA/SDI)
unnamed: R7.1, U2.14 (*RST)
unnamed: C10.1, U2.13 (C)
unnamed: C10.2, U2.11 (C+)
unnamed: C11.1, U3.10 (REGOUT)
enab: ESP32_QT_PY1.11 (MO), IC1.7 (EN), IC2.7 (EN), R11.1
scl: ESP32_QT_PY1.6 (SCL), NT1.1
sda: ESP32_QT_PY1.5 (SDA), NT2.1
servopower: J2.2, J3.2, J4.2, J5.2, U1.1 (vout)
uart: ESP32_QT_PY1.10 (MI), IC1.10 (~PD_UART/HS_PWM), IC2.10 (~PD_UART/HS_PWM)
vbat: C2.1, C3.1, C6.1, C13.1, C16.1, C17.1, C18.1, IC1.18 (VS), IC2.18 (VS), J1.2, R1.1, U1.3 (vin), U2.5 (SEL2), U2.6 (VIN), U2.9 (VIN)

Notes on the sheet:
addr

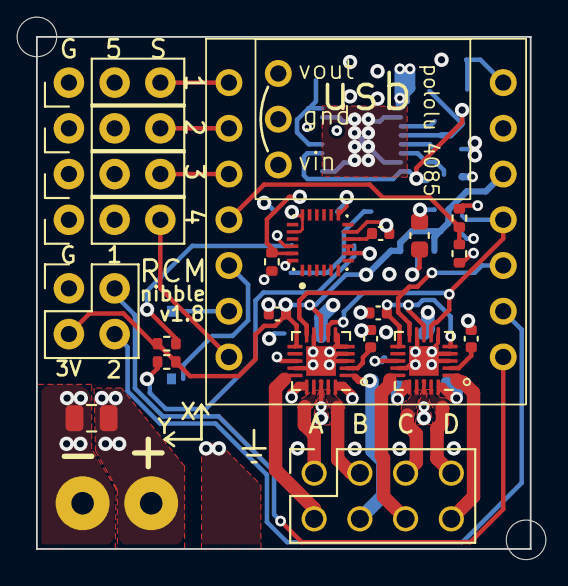
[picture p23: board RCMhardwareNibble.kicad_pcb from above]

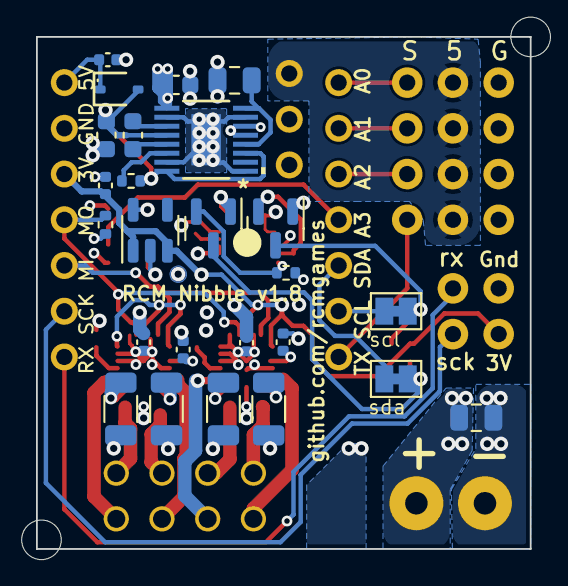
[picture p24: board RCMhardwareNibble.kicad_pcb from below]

Board: 4 copper layers, 27.4 x 28.4 mm, 51 parts (25 on the bottom side), 43 nets.

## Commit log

2024-04-16 close #3 close #4
    [BOM-RCM-Nibble-v1.5.csv, RCMhardwareNibble.kicad_pcb, RCMhardwareNibble.kicad_sch]
2024-05-07 working on v1.7
    [BillOfMaterials - RCMhardwareNibble - v1.6.csv, RCM-Nibble.3mf, RCM-Nibble.stl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]
2024-05-15 update production files
    [BOM-RCMhardwareNibble-v1.7.csv, RCMhardwareNibble.kicad_pcb, RCMhardwareNibble.kicad_sch]
